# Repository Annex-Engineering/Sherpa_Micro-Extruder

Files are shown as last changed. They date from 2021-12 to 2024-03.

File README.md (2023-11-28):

## Sherpa Micro - Release 2

This release adds support for Bondtech's RIDGA v2 in addition to numerous tweaks and updates to make the extruder easier to work on and more reliable than ever.

## Changelog

+ Bondtech RIDGA v2 compatibility (R2 RC1 and newer)
+ Bondtech insert support
+ Stronger and stiffer idler arm
+ Increased clearance between idler arm and core
+ Minor fixes and adjustments in preparation for upcoming upgrades

+ Core housing and rear housing need to be reprinted if upgrading from Release 1
+ Updated idler arms are backwards compatible with Release 1 and Release 2 RC1

## Micro Fixed Idler Public Alpha:
+ Bondtech RIDGA v2 compatibility
+ Fixed idler version of the Micro, based on @churls' work
Experimental design, not recommended for production use
Please provide feedback on the Annex discord server if you encounter issues

## FAQ
For Material Requirements, Print Settings and How to Interpret the file naming structure, please see: "Print_Settings_and_File_Key.txt"

The BOM and Sourcing Guide for this product can be found here: https://docs.google.com/spreadsheets/d/1O3eyVuQ6M4F03MJSDs4Z71_XyNjXL5HFTZr1jsaAtRc/edit?usp=sharing

## Product Info & Support
This is the Sherpa Micro Extruder, a ground up design developed by Anlin and the team at Annex Engineering. It's a dual geared hobbed filament extruder designed for use with any printer. It features a gear driven design to provide torque while being able to be near silent. You must perform your own tuning to get the best results.

A Pinion Equipped Pancake Stepper is required for this Release.

Join me on Discord (https://discord.gg/MzTR3zE)

Please only use GitHub Issues for repo and file related problems. For general design related questions and technical support please visit our Discord server.

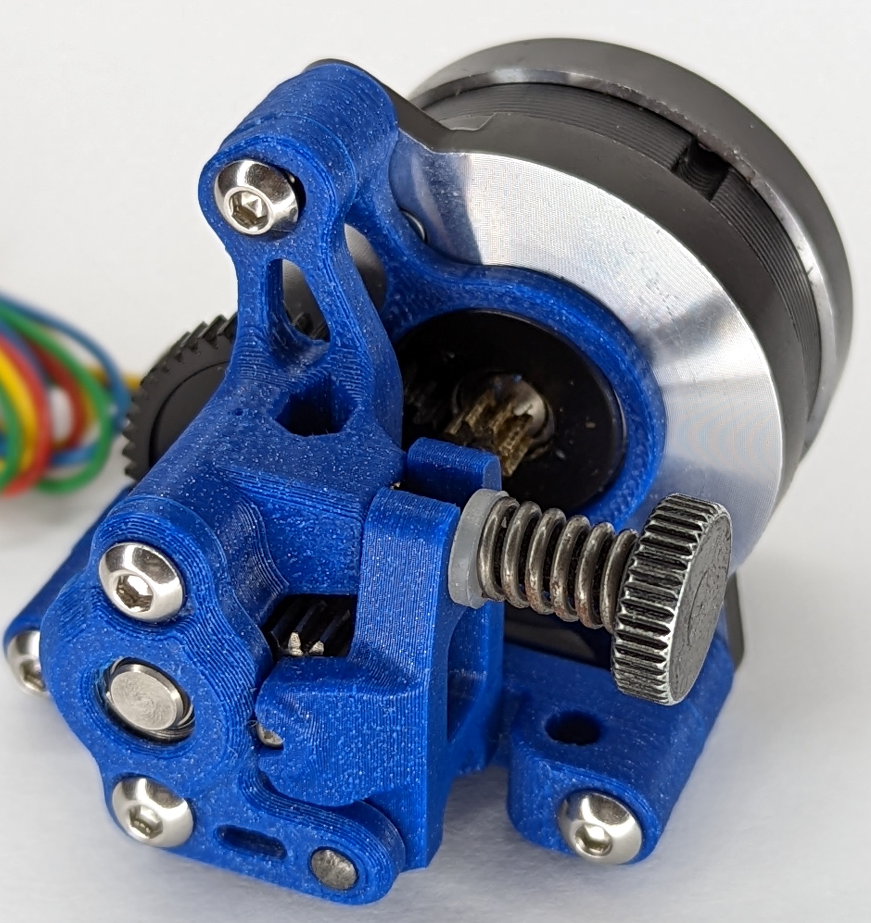
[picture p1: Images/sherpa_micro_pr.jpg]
Image of Sherpa Micro Extruder


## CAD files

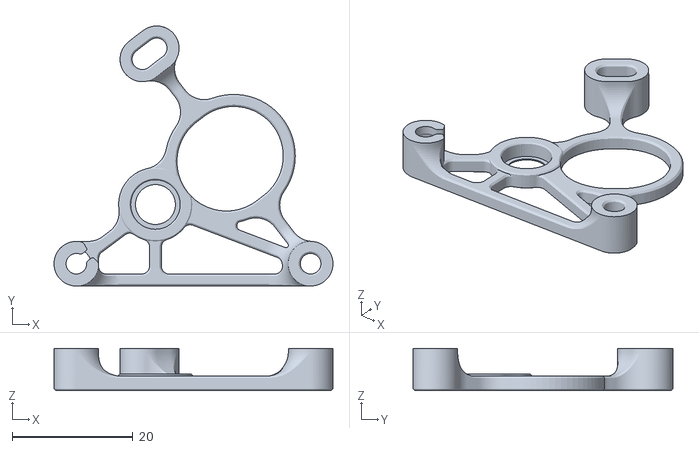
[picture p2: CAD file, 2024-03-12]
STLs/micro_fixed_alpha_1/housing_rear_x1_rev9.STL
46.2 x 43.1 x 7.00

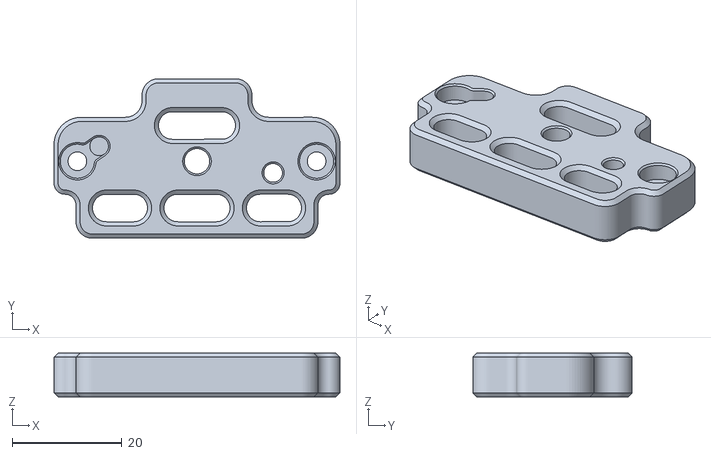
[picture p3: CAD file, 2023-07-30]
STLs/micro_fixed_alpha_1/optional_parts/mini_adapter_x1_rev1.STL
52.0 x 29.0 x 8.00

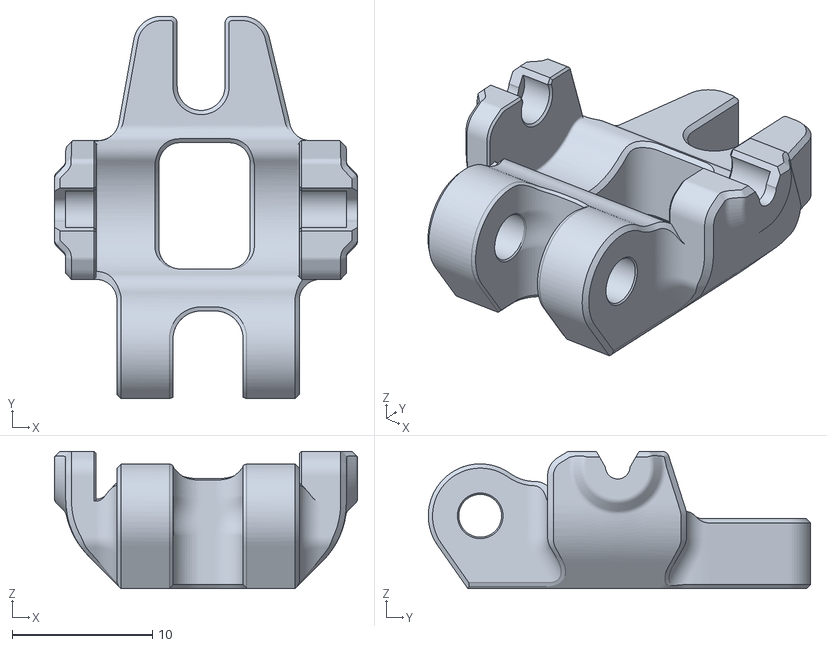
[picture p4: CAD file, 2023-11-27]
STLs/micro_standard_r2/optional_parts/[a]_idler_arm_short_x1_rev8a.STL
21.6 x 27.3 x 9.80

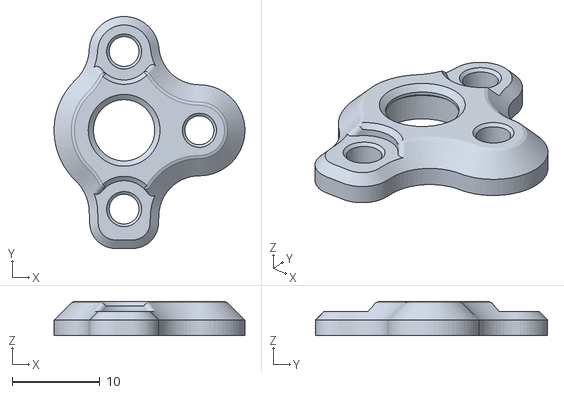
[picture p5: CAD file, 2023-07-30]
STLs/micro_fixed_alpha_1/[a]_housing_front_x1_rev1.STL
21.8 x 26.5 x 3.90

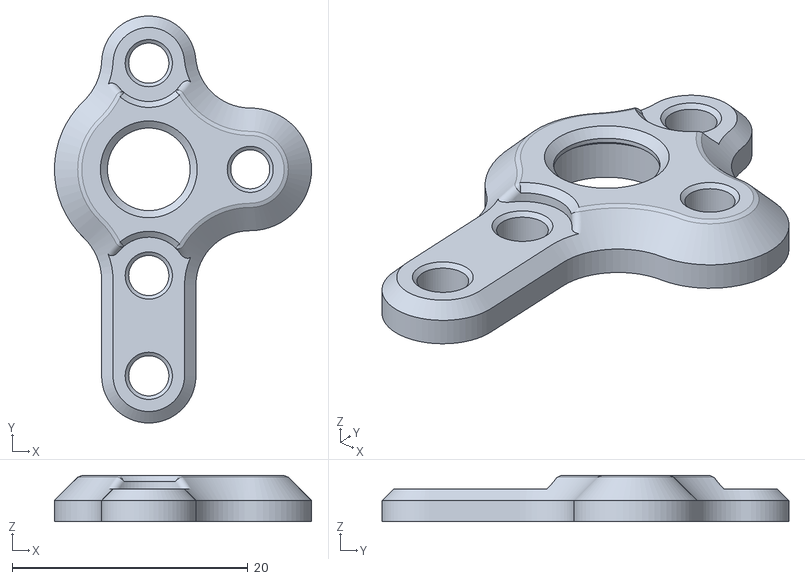
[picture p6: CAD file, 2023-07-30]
STLs/micro_fixed_alpha_1/optional_parts/[a]_housing_front_k_x1_rev1.STL
21.8 x 34.5 x 3.90

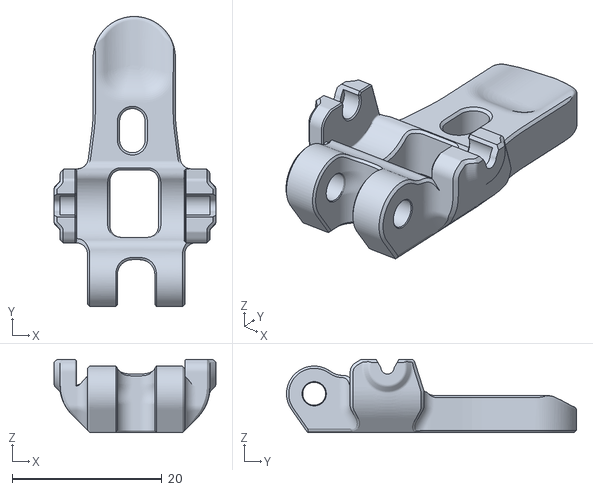
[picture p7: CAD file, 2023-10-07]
STLs/micro_standard_r2/[a]_idler_arm_long_x1_rev8a.STL
21.6 x 38.8 x 9.80

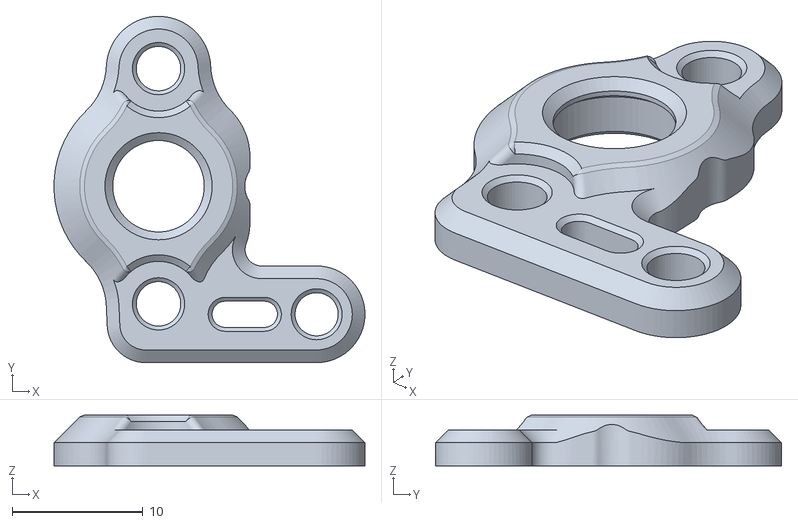
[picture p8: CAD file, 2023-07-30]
STLs/micro_standard_r2/[a]_housing_front_x1_rev7.STL
23.8 x 26.5 x 3.90

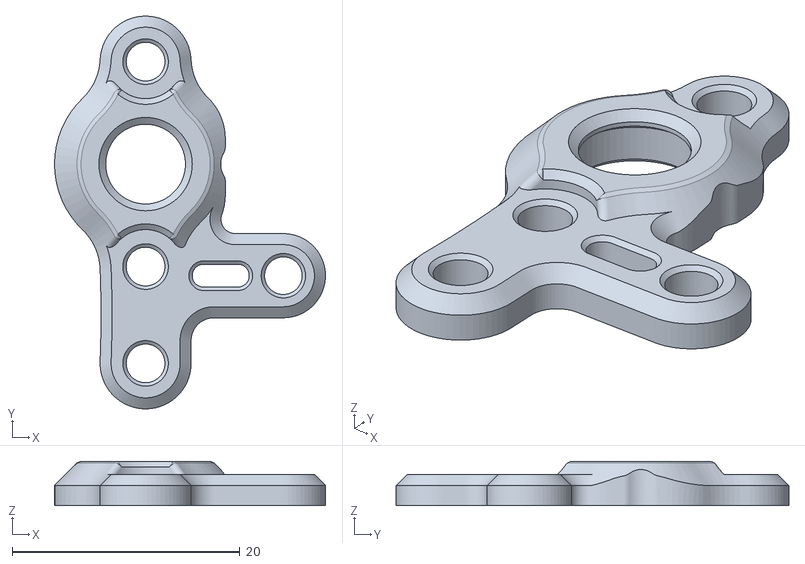
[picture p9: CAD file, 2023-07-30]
STLs/micro_standard_r2/optional_parts/[a]_housing_front_k_x1_rev7.STL
23.8 x 34.5 x 3.90

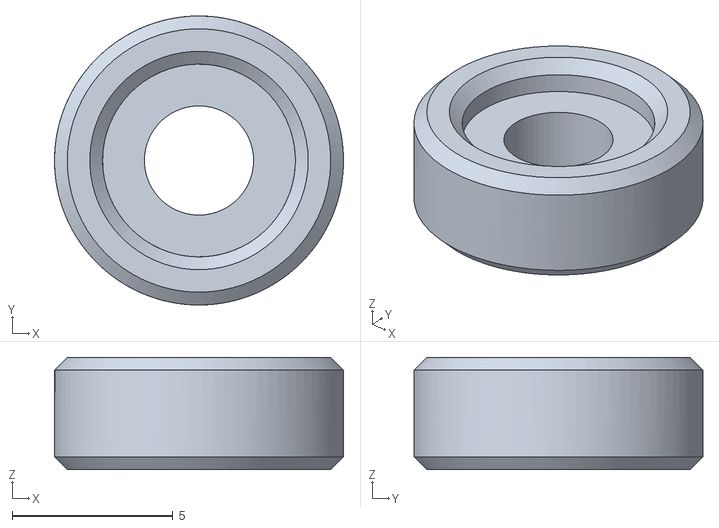
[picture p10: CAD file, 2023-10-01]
STLs/micro_standard_r2/optional_parts/[a]_bondtech_thumbscrew_spacer_x1_rev1.STL
9.00 x 9.00 x 3.50

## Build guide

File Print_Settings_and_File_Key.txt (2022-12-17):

Primary Color: nothing at start of file name
Accent Color: [a]_ at start of file name
Quantity Required: _x# near end of file name
File Revision: _Rev# at end of file name

Nozzle Size: 0.5mm 
Recommended FDM Materials: ASA, Polymaker or 3DXTech Recommended
Alternate Approved FDM Materials: PC, 3DXTech Recommended
Layer Height: 0.25mm
Extrusion Width: Forced 0.5mm
Infill Percentage: 40% minimum (at 0.8mm Width)
Infill Type: Grid, Gyroid, Honeycomb, Triangle or Cubic
Wall Count: 3 minimum (at 0.5mm Width)
Solid Top/Bottom Layers: 4 minimum (at 0.5mm Height)

Nozzle Size: 0.4mm 
Recommended FDM Materials: ASA, Polymaker or 3DXTech Recommended
Alternate Approved FDM Materials: PC, 3DXTech Recommended
Layer Height: 0.20mm or 0.25mm
Extrusion Width: Forced 0.4mm
Infill Percentage: 40% minimum (at 0.6mm Width)
Infill Type: Grid, Gyroid, Honeycomb, Triangle or Cubic
Wall Count: 4 minimum (at 0.4mm Width)
Solid Top/Bottom Layers: 4 minimum (at 0.25mm Height)

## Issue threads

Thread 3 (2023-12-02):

use with AfterSherpa

FkYeahScience, 2023-12-02:
no adapter or a modified toolhead STL, can you provide this in the future?

anlin93, 2024-02-28:
Both of the requested designs are outside of the scope of this project

Closed 2024-02-28.

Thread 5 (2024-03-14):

Filament gears offset

propeller3D, 2024-03-14:
I'm looking in the sherpa micro CAD and I'm looking into the alignment of the filament gears and it's looking like in the picture. To me this looks lke the gears are going to bite into the filament too much.  If you open it up more then the hole the filament passes through will be offset. The blue circle is 1.75mm in diameter. Is this right? How much do the gears bite into the filament? I'm thinking this should be adjusted a bit. I was thinking the hole tolerances maybe will make it more offset to the left but the holes are holding bearings and those are press fit.
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

propeller3D, 2024-03-14:
It's possible this has been extensively tested and concluded that this is the best position for it but it seems a bit harsh to expect the filament to be mangled 0.4mm on each side. The VZ hextrudort seems to have about 1.1mm between the teeth vs 0.9mm for the sherpa. This is likely a non issue just raising the question to be thorough.

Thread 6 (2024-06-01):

A little bit of documentation for the fixed idler version

KlausHans, 2024-06-01:
I am really interested in the fixed idler version. Unfortunately i can find nothing on the internet to this. Not even a photo.

Can you please provide a image of it and maybe some short notes for assembly?

Thank you very much.

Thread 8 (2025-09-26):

Problem with the STEP and the STL files

sverd, 2025-09-26:
I'm trying to integrate a small filament motion sensor into the micro extruder (to keep things really compact).  To accomplish that I tried to use the step and/or the stl files as starting point in FreeCAD.  These files import nicely, but seem to contain some problems which prevent me to adjust anything.
Is this a known problem with FreeCAD or could it be that something is sub-optimal with the STEP and STL files?

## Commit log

2021-12-16 initialize repo
    [Klipper_Config_Block.txt]
2022-01-01 add stls and edrawings for alpha 1
    [housing_front_k_x1_rev1.STL, housing_front_x1_rev1.STL, housing_rear_x1_rev1.STL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]
2022-01-01 add accent color callouts
    [[a]_housing_front_k_x1_rev1.STL, [a]_housing_front_x1_rev1.STL, [a]_idler_arm_long_x1_rev1.STL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]
2022-03-03 fix print orientation of mini adapter
    [mini_adapter_x1_rev1.STL]
2022-03-24 add release1 stuff
    [[a]_housing_front_k_x1_rev1.STL, [a]_housing_front_k_x1_rev2.STL, [a]_housing_front_x1_rev1.STL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]
2022-05-27 add retraction notes to config
    [Klipper_Config_Block.txt]
2023-07-30 r2 rc for std, and r1 a1 for fixed
    [[a]_housing_front_k_x1_rev1.STL, [a]_housing_front_k_x1_rev2.STL, [a]_housing_front_k_x1_rev7.STL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]
2023-10-07 fixed export of stl, reprint recommended
    [[a]_idler_arm_long_x1_rev8.STL, [a]_idler_arm_long_x1_rev8a.STL]
2023-10-27 migrate printer, extruder and board configs to an MIT licensed repo
    [Klipper_Config_Block.txt]
2023-11-27 cad and shiz
    [[a]_idler_arm_short_x1_rev8.STL, [a]_idler_arm_short_x1_rev8a.STL]
2023-12-02 Rename CAD file
2024-03-12 Release 2 rev 1
    - Reduced rear housing spacer ring thickness (fixes RIDGA alignment)
    - CAD in STEP format
    - Removed Bondtech specific housing STLs (new kits come with standard inserts)
    [housing_rear_bondtech_inserts_x1_rev8.STL, housing_rear_x1_rev1.STL, housing_rear_x1_rev7.STL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]
